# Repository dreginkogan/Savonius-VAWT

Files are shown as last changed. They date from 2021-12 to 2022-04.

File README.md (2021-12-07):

# VAWT #

<p align="center">
  
</p>

## What is a VAWT? ##

"A vertical-axis wind turbine (VAWT) is a type of wind turbine where the main rotor shaft is set transverse to the wind (but not necessarily vertically) while the main components 
are located at the base of the turbine. This arrangement allows the generator and gearbox to be located close to the ground, facilitating service and repair. VAWTs do not need to 
be pointed into the wind, which removes the need for wind-sensing and orientation mechanisms. Major drawbacks for the early designs (Savonius, Darrieus and giromill) 
included the significant torque variation or "ripple" during each revolution, and the large bending moments on the blades. Later designs addressed the torque ripple issue by
sweeping the blades helically (Gorlov type). Savonius vertical-axis wind turbines (VAWT) are not widespread, but their simplicity and better performance in disturbed 
flow-fields, compared to small horizontal-axis wind turbines (HAWT) make them a good alternative for distributed generation devices in urban environment." - Wikipedia

This wind turbine is specifically a Savonius wind turbine

"The Savonius turbine is one of the simplest turbines. Aerodynamically, it is a drag-type device, consisting of two or three scoops. Looking down on the rotor from above, a two-scoop machine might resemble the letter "S" in cross section. Because of the curvature, the scoops experience less drag when moving against the wind than when moving with the wind. The differential drag causes the Savonius turbine to spin. Because they are drag-type devices, Savonius turbines extract much less of the wind's power than other similarly-sized lift-type turbines. In practice, much of the swept area of a Savonius rotor may be near the ground if it has a short mount without an extended post, making the overall energy extraction less effective due to the lower wind speeds found at lower heights." - Wikipedia

## Project ##

I am trying to create a single-stage Savonius VAWT out of 3D-printed parts and recycled soda cans. 

## Design CAD files ##

There is a .step file attached

## Turbine Blades ##

Due to the interchangeable nature of the rotor, it is also possible to create a different kind of VAWT, not just Savonius. Any other type of VAWT rotor can be attached to the shaft of the turbine.

## Google sheets ##

https://docs.google.com/spreadsheets/d/15GiFD8pNvUtQi8-LZ8H8-wIT5L8Z5X-Vn8ogBe61qog/edit?usp=sharing

In order for the generator to be effective, a bridge rectifier is needed. 
Details for its creation can be found in this video: https://www.youtube.com/watch?v=-zCTggoh994

## Assembly ##

Most assembly can be figured out by looking at the CAD files. For parts that aren't attached together with screws, hot glue/superglue/high friction materials may be used. I personally used a lot of hot glue, but that may not be the most effective. I will eventually provide more documentation on assembly.

For assembling each turbine blade, refer to https://github.com/dreginkogan/Savonius-VAWT/blob/main/blade_assembly.md.

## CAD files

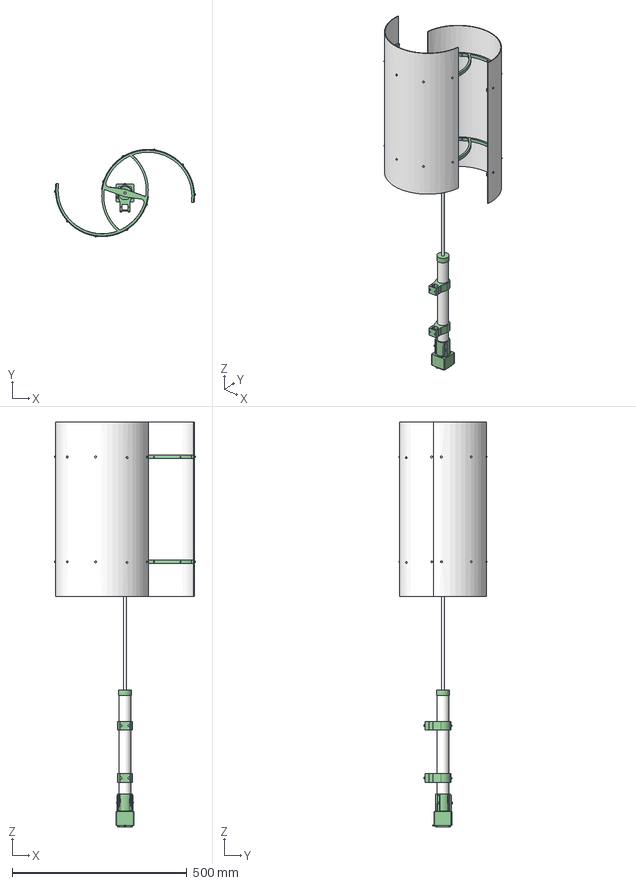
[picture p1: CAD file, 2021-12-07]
turbineAssembly.step
404.2 x 253.1 x 1159.0 mm
bearing608 x 2
bearingSleeve x 2
pipe
pipeEndCap
stepperMount
Frontplate
Backplate
Connenctor
Housing
Bearing dummy
Bearing dummy 01
Core_1
Cable
M3x34-Screw x 4
motorToAxleCoupler
M3x6mm x 24
shaft
M3x12mm x 3
M3x16mm x 4
M3x10mm x 2
largeSemiBlade x 2

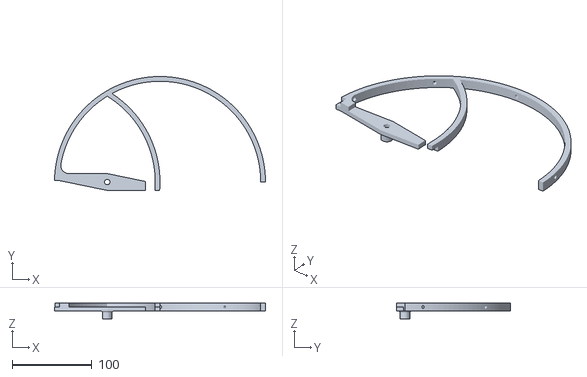
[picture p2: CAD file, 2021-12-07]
ribSplit1.stl
264.0 x 142.6 x 20.0

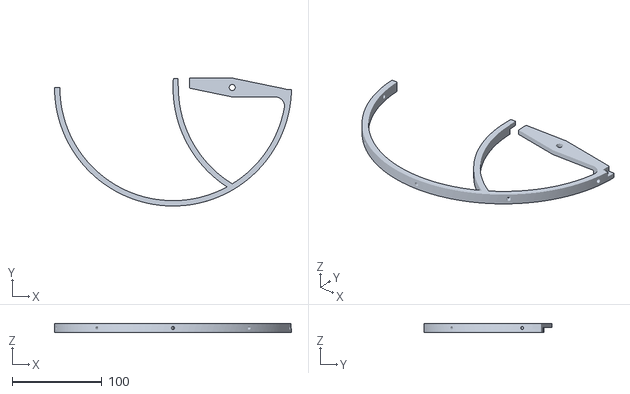
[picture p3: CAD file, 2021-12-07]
ribSplit2.stl
264.0 x 142.6 x 10.0

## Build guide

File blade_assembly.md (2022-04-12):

# Blade assembly instructions

- Note: this is for the metal parts of the turbine blades. These instructions don't include how to attach it to the rest of the turbine. For that, look at the cad files.

### Materials needed

- 12x aluminum cans (large blade) || 6x aluminum cans (small blade)
- Aluminum tape
- Duct tape
  
### Assembly

1. Turn soda cans into sheets (this tutorial can help: https://craftyjournal.com/how-to-turn-a-soda-can-into-a-flat-sheet-of-aluminum/)
2. Tile the sheets together into a 2x6 arrangement for a large blade, or 1x3 for a small one. (horizontal x vertical)
3. Tape the sheets together using aluminum tape. Be sure to cover the gaps between them on both sides.
4. Due to imperfections in cutting the aluminum (unless you've done it perfectly), there may be bumps on the blade. In order to "get rid of" them, you can smoosh them down with someting heavy.
5. Cover the edges and the interior face (the blade will try to curl inwards once you tape the cans together) of the blade with duct tape.
6. Repeat these steps a second time, in order for you to have two blades.

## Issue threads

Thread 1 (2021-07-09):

Unstable blades

dreginkogan, 2021-07-09:
This turbine is exposed to the elements, day and night, so of course it would have to face heavy winds and rain. A problem with the turbine is that the cans sometimes fall off. I am not using any fasteners, only hot glue and superglue.

A potential fix to this is either just gluing better, or creating a way that the cans stay in place mechanically.

Closed 2021-07-14.

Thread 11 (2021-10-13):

blades aren't stable

dreginkogan, 2021-10-13:
Attaching blades to the ribs with hot glue is unstable, as they can easily fall off. I need to design some way to attach them with screws.

dreginkogan, 2021-11-27:
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

Closed 2021-12-07.

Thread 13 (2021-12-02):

Use screws to secure blades to ribs.

dreginkogan, 2021-12-02:
The only issue with this is that extra weight may be added, but it will be very slight either way.

Closed 2021-12-07.

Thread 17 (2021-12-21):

Central shaft weak

dreginkogan, 2021-12-21:
Using screws to attach the blades to the ribs was effective, and there are no longer issues where they break off from the device. However, the damage that would have happened there is transferred to the axle, which bends.

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

A possible solution to this issue is to get a shaft made out of a material like steel or carbon fiber.

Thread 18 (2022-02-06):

reorganize cad

dreginkogan, 2022-02-06:
Currently, all the CAD stuff is done in like 500 different files, which makes working on the CAD a pain. Fusion 360 is good for making entire assemblies in a single file, so I should go ahead and do that.

dreginkogan, 2022-02-17:
What I mean is to make everything parametric instead of direct.
